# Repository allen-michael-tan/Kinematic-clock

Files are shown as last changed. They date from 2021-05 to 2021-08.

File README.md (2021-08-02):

# Kinematic Clock

This repository showcases how Singapore Polytechnic MakerSpace's kinematic clock was made.  

The design follows the Clockception instructables guide made by [madebymorgan](https://www.instructables.com/Clockception-How-to-Build-a-Clock-Made-From-Clocks/), where some aspects of the design were modified. 

## 3D Design

Before fabrication, all components were modelled in Autodesk Inventor Professional. The inventor files can be found [here](https://github.com/allen-michael-tan/Kinematic-clock/tree/main/Inventor%20files)

In this design, each digit will be represented using 6 individual smaller clocks, 24 clocks were needed to display 4 digits. The colour scheme used in the design is black and white.

### Clock design

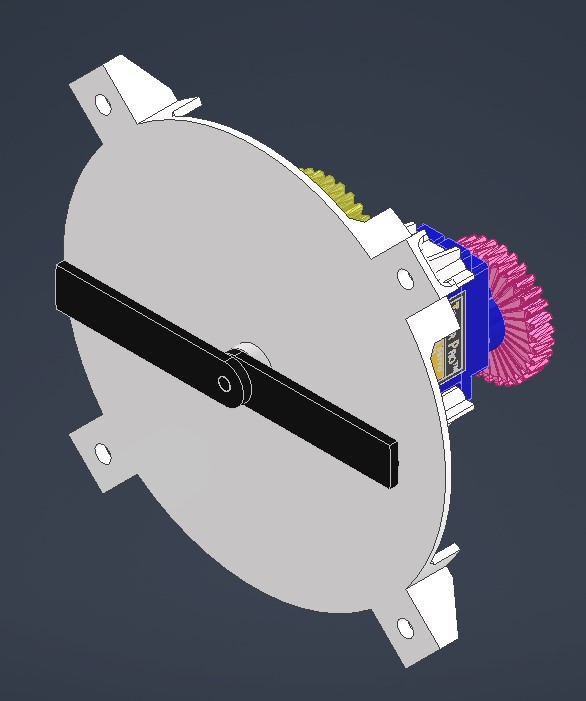
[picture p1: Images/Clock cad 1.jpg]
Clock cad 1
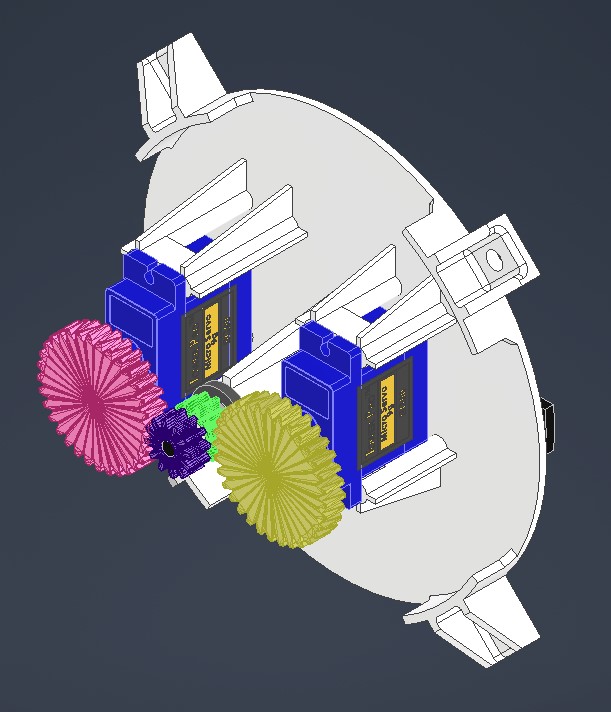
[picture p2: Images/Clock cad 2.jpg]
Clock cad 2
 

The design of the individual clock bodies is shown above. 

### Board design

In addition to having a board to mount the clocks onto, 4 smaller boards are included in the design to raise the board forward, giving it a floating illusion when mounted onto a wall. 

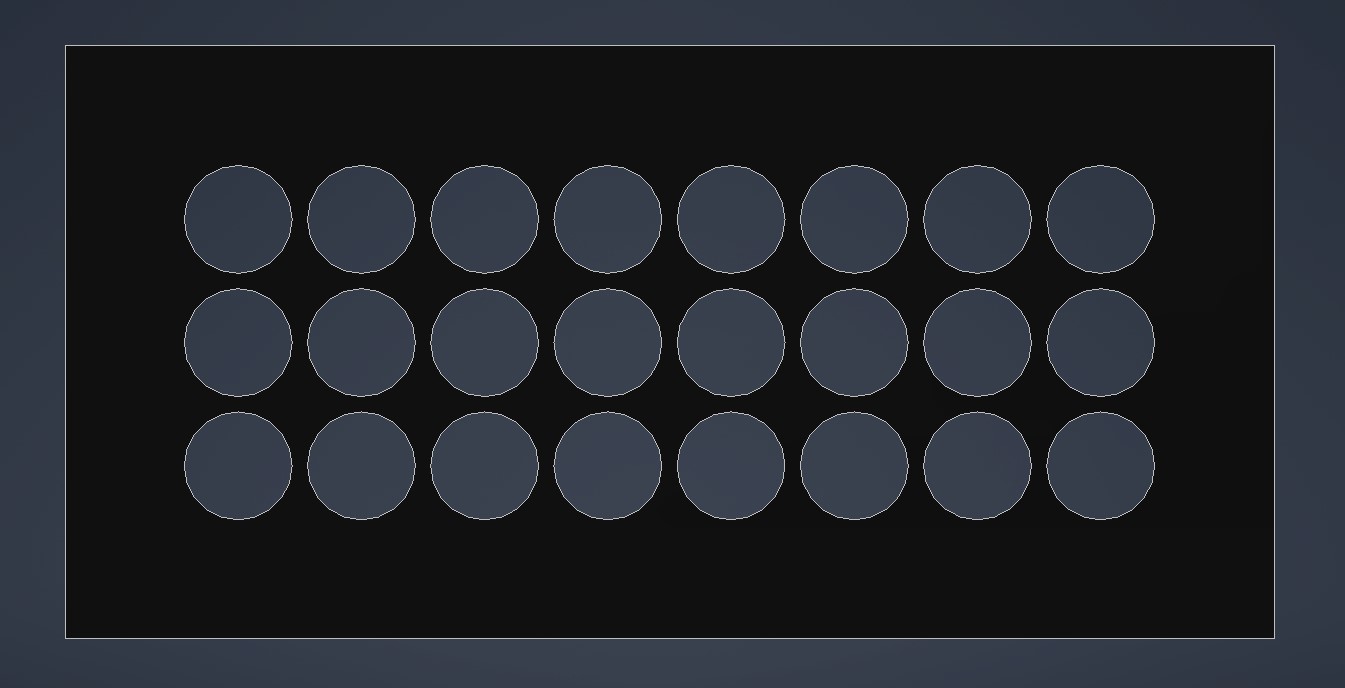
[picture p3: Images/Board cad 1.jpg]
Board cad 1


This is the front view of the board. 

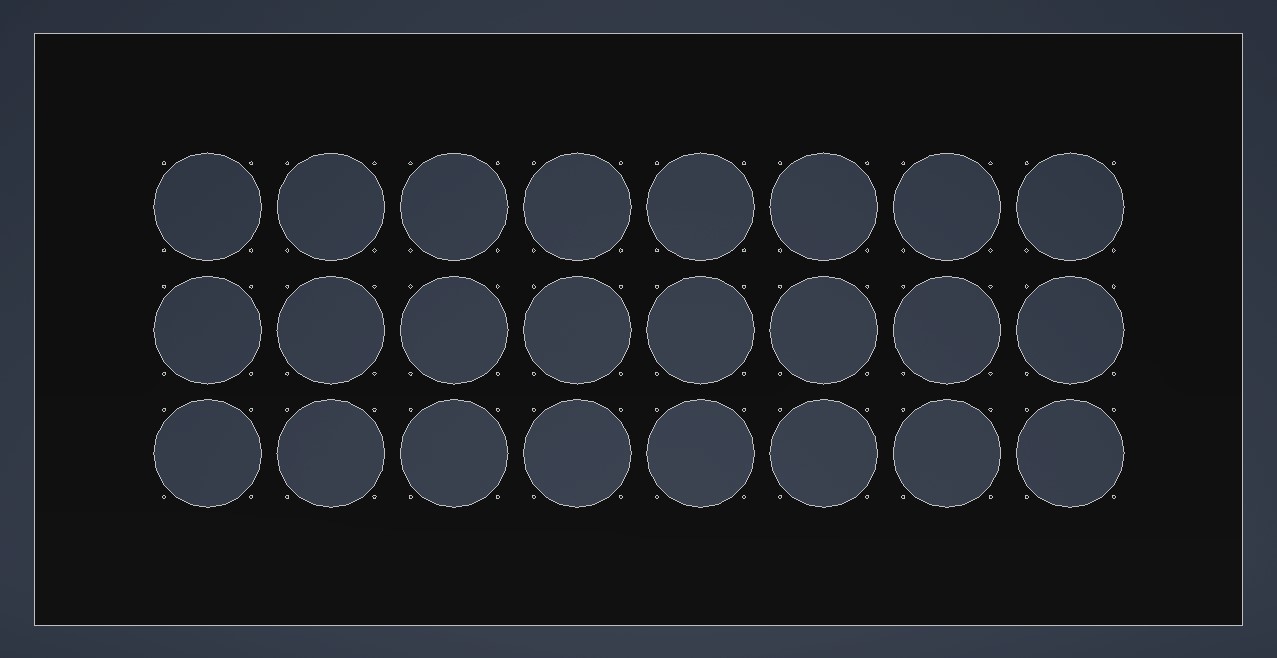
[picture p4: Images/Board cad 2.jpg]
Board cad 2


This is the back view of the board.

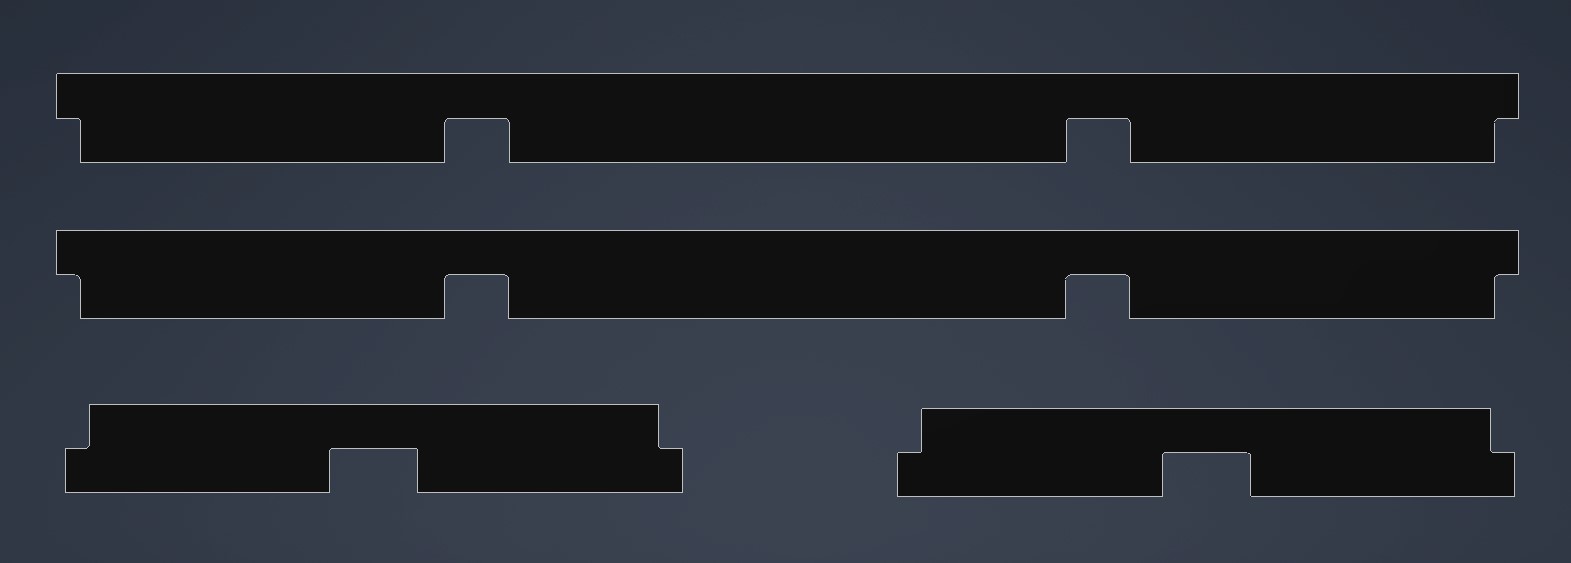
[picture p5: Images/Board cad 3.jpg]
Board cad 3


These are the smaller boards attached to the back of the main board, they are offseted inwards to give the floating illusion when the board is mounted onto a wall.

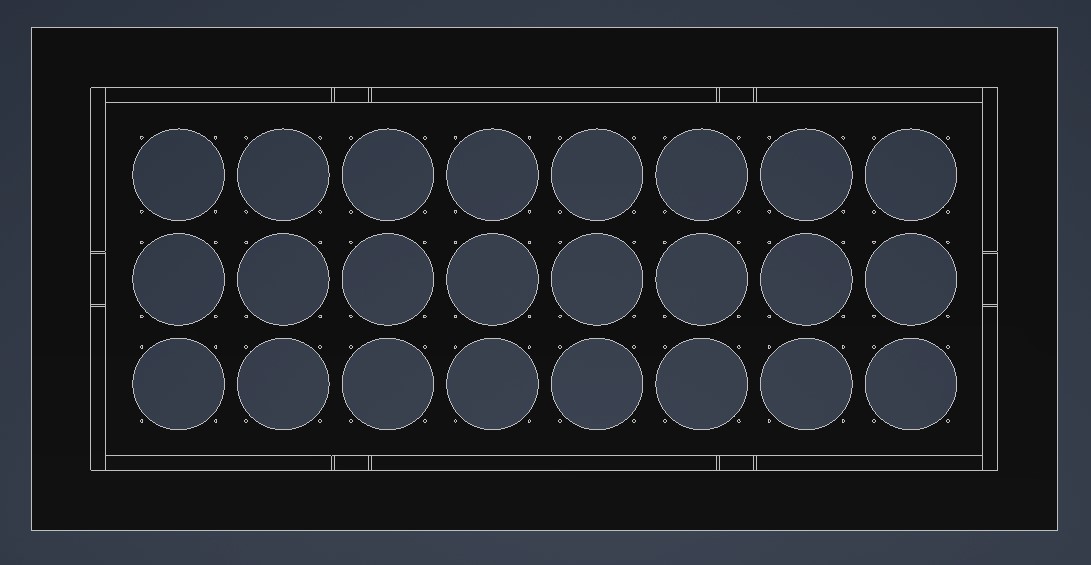
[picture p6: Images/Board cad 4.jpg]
Board cad 4


The above shows the assembly of the smaller boards onto the back of the main board. In the actual piece, they will be screwed into the main board using self tapping wood screws and L brackets. 

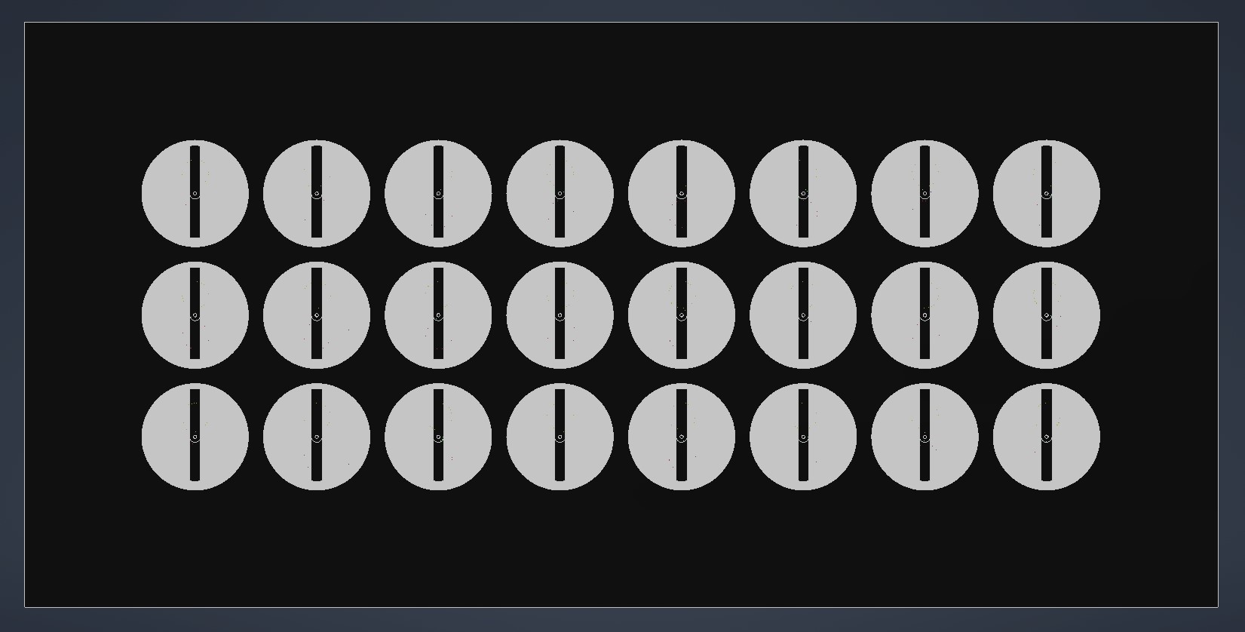
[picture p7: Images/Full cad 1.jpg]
Full cad 1


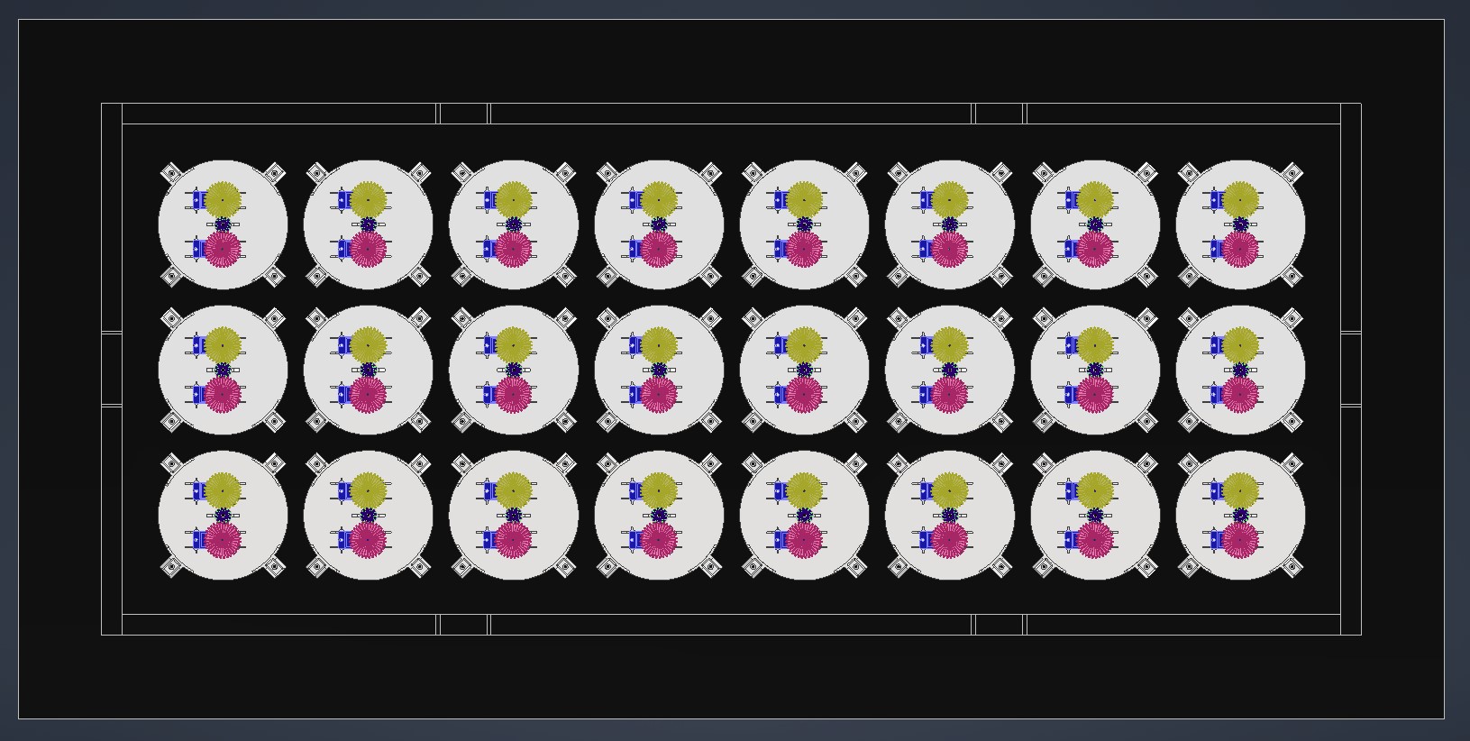
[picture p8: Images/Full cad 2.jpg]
Full cad 2


The above shows the respective front and back views of the full assembly of the kinematic clock in 3D CAD.

## Clock Assembly
Each clock is made up of: 

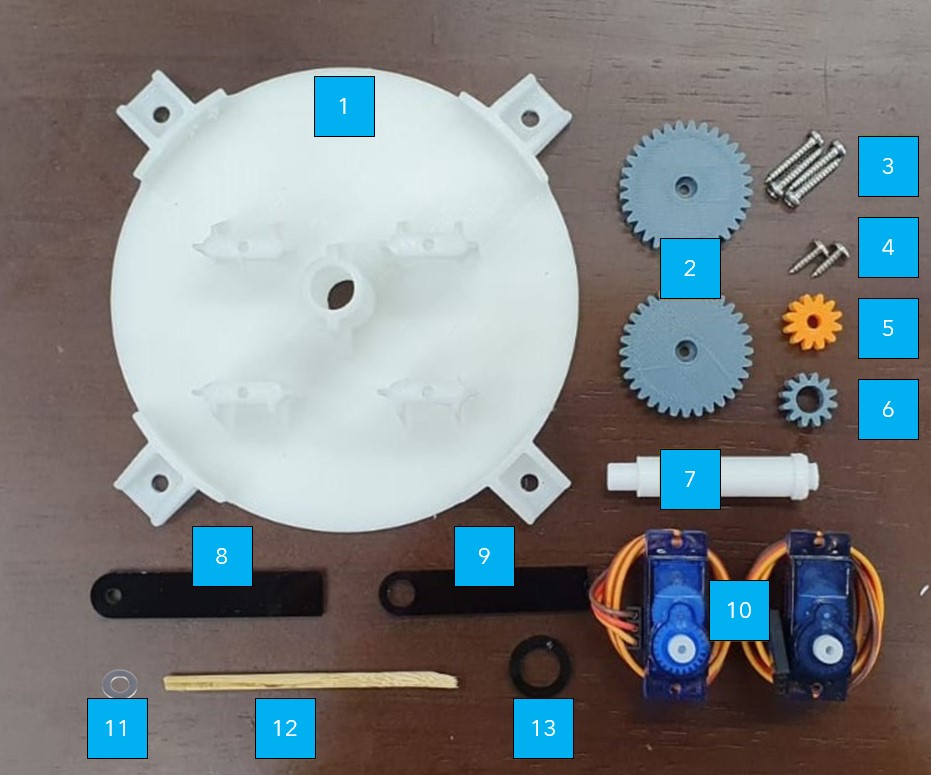
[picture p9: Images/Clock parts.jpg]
Clock parts


1. Clock body [1]
2. Servo gear [2]
3. M2x12 pan head self-tapping screw [4]
4. M2x8 flanged pan head self-tapping screw [2]
5. Minute hand gear [1]
6. Hour hand gear [1]
7. Hour hand shaft [1]
8. Minute hand [1]
9. Hour hand [1]
10. Continuous servo motor [2]
11. M3 plain washer [3]
12. Bamboo skewer [1]
13. Retaining ring [1]  

### Parts manufacturing

The components of each clock were created using 3D printers, laser cutters and vinyl stickers.

#### 3D print

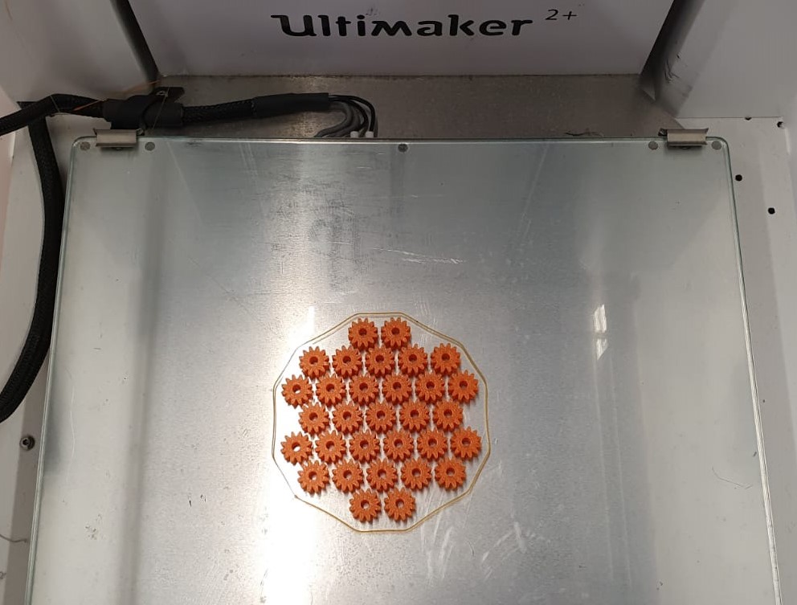
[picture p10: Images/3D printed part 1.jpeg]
3D printed part 1


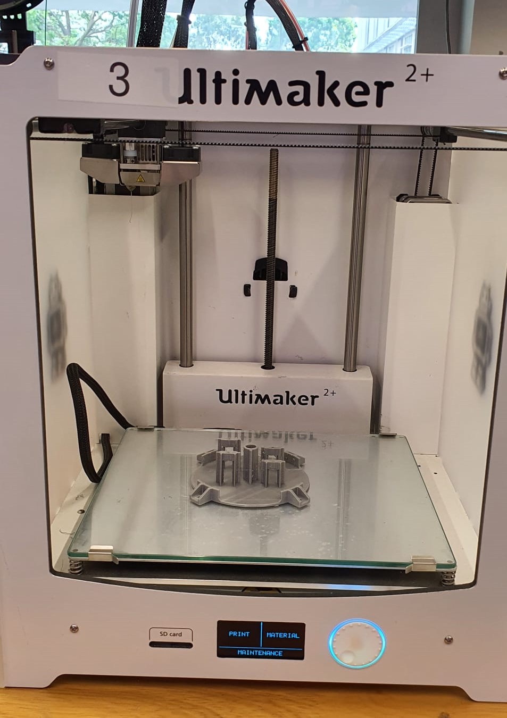
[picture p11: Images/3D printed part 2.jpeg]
3D printed part 2


Majority of the clock parts were 3D printed with PLA material.

#### Laser cut

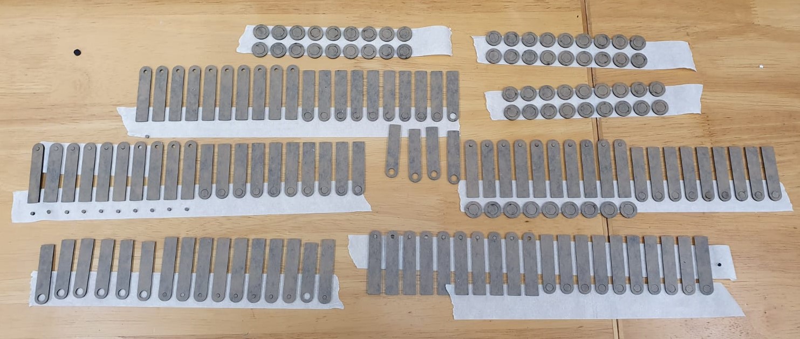
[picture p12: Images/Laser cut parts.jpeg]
Laser cut parts


Flat parts such as clock hands and hour retaining ring were made with laser cut 2mm black coloured acrylic. 

#### Vinyl sticker

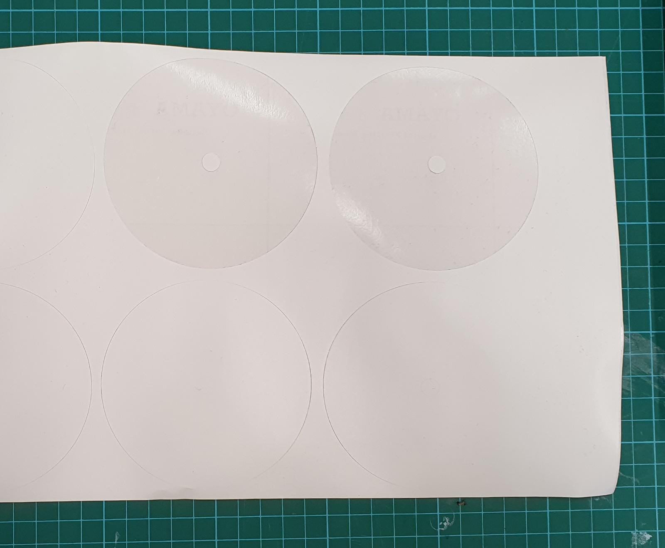
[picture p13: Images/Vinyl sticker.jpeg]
Vinyl sticker


In order to allow for uniformity across all the clock faces, white vinyl stickers were cut and applied onto each clock face. 

### Pre-assembly preparation

Before each clocks were put together, some components of the clock had to be prepared first.

#### Coating of 3D printed parts

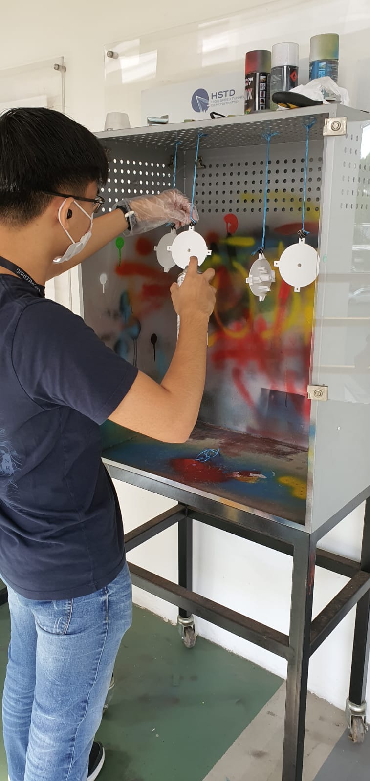
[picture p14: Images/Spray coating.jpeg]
Spray coating


The material used for all 3D printed parts was PLA. This material has the tendency to disintigrate after a period of time, so a clear coat was applied on all the printed parts to increase their longevity. 

#### Hour hand assembly

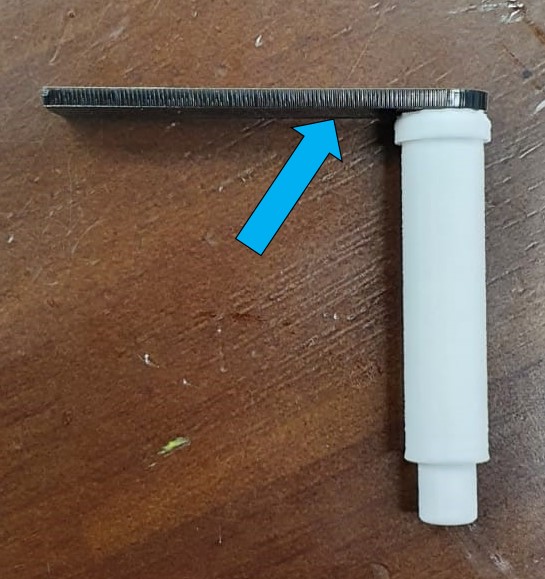
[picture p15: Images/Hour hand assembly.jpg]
Hour hand assembly


The laser cut hour hand (blue arrow) was superglued to the tip of the hour hand shaft as shown above.

#### Minute hand assembly

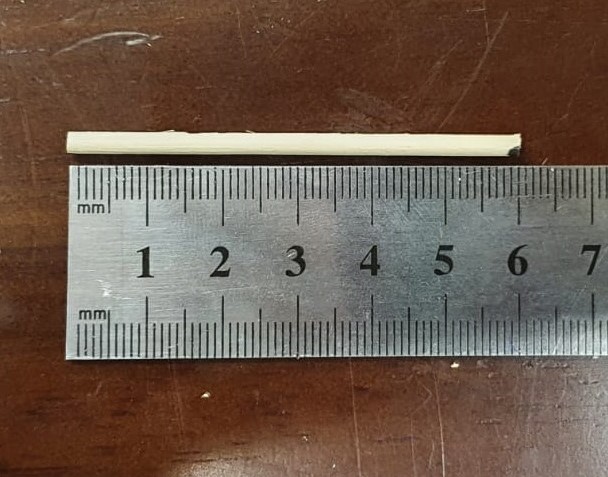
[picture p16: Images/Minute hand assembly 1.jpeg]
Minute hand assembly 1


3mm thick bamboo skewers were cut into lengths of 60mm.

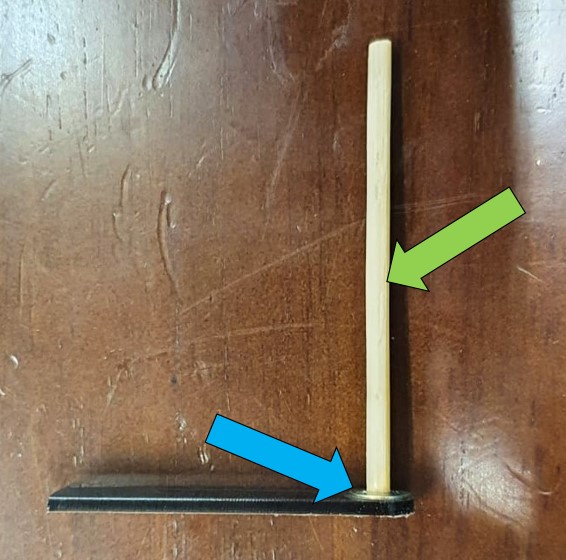
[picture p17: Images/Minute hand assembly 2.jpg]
Minute hand assembly 2


M3 plain washer was superglued to the underside of the laser cut minute hand (blue arrow), this is done so to minimize friction between the minute and hour hand as they rotate. 

After which, a bamboo skewer was inserted to the minute hand and superglued (green arrow).

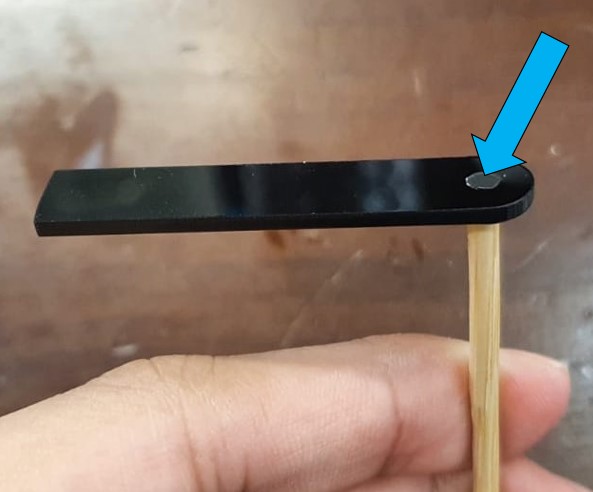
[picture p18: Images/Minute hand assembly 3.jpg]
Minute hand assembly 3


Lastly, on the other side of the minute hand where the bamboo skewer was inserted, black paint is applied onto the exposed side of the skewer (blue arrow). 

### Assembly

#### Step 1

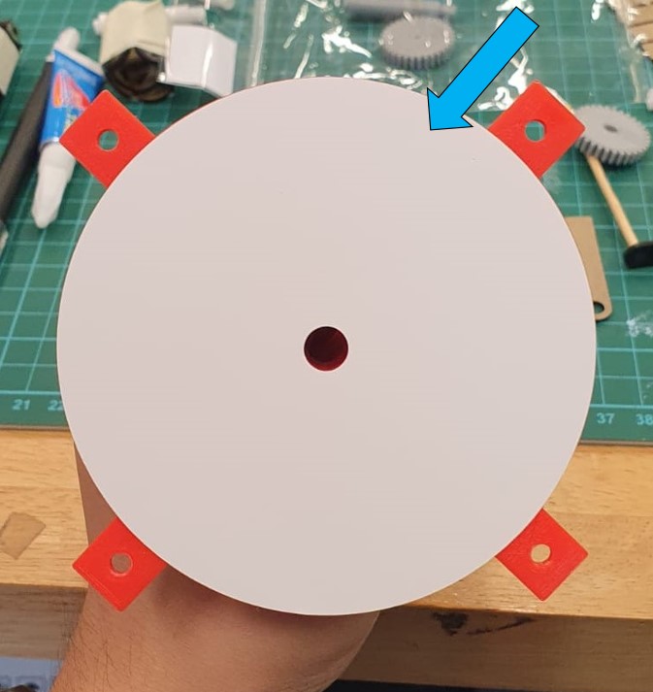
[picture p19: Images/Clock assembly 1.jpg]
Clock assembly 1


The colour theme of the clock was black and white - black board and clock hands, white clock face. As the clock bodies were printed in different colours, white vinyl stickers were cut out and pasted onto the outside face of the clock body (blue arrow). 

*****

#### Step 2

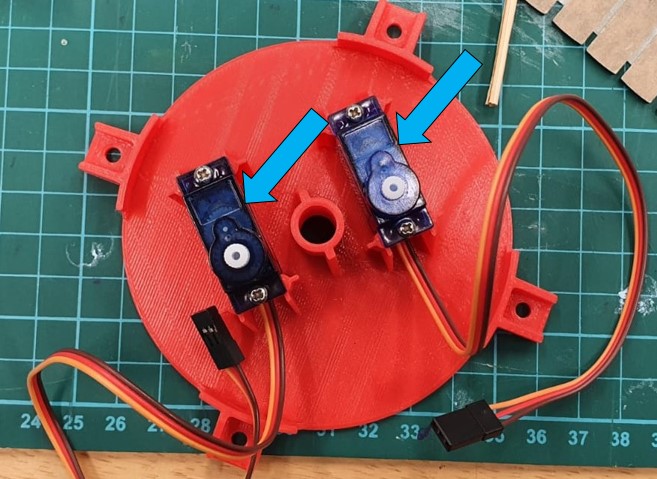
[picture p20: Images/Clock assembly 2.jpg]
Clock assembly 2


Next, two continuous servo motors were installed onto the clock body as shown above and secured using 4 screws (blue arrows).

*****

#### Step 3

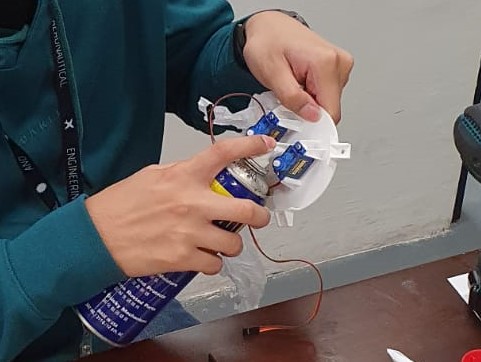
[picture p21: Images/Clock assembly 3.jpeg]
Clock assembly 3


Before inserting the hour hand, the shaft hub was lubricated using WD 40 to reduce friction between the hour hand shaft and the clock body.

*****

#### Step 4

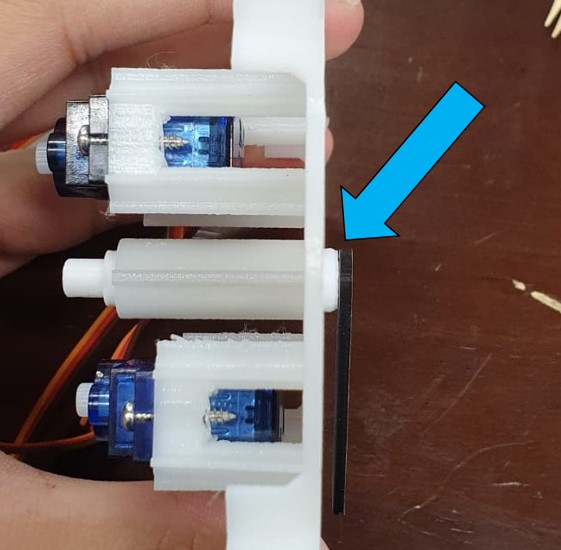
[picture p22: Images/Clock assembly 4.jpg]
Clock assembly 4


The hour hand was inserted as shown (blue arrow). 

*****

#### Step 5

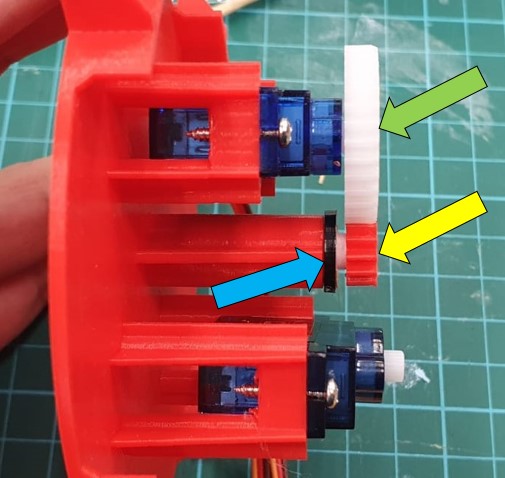
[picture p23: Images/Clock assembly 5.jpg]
Clock assembly 5


After the hour hand has been inserted, a retaining ring (blue arrow) was inserted as shown to prevent he hour hand from falling off. 

Following that, the hour hand gear (yellow arrow) and a servo gear (green arrow) was assembled accordingly. Then, a screw is used to secure the servo gear to the servo motor. 

*****

#### Step 6

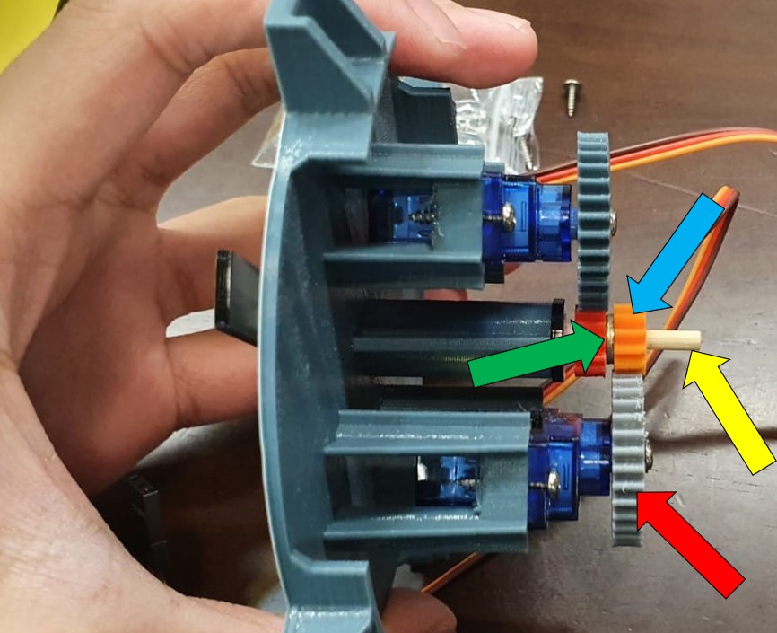
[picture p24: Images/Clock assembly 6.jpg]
Clock assembly 6


In this final step, the minute hand (yellow arrow) was inserted into the hour hand shaft, followed by two washers (green arrow) and minute hand gear (blue arrow).

It is important to note that, the before inserting the minute hand gear, the bamboo skewer should rotate freely with little friction whilst inserted in the hour hand shaft. This is because if there was too much friction, when the hour hand rotates, the minute hand will rotate along it which is undesired. 

The purpose of the washer is to prevent the bamboo skewer from jiggling in and out the hour hand shaft.

Lastly, a second servo gear (red arrow) is secured to the second servo motor with a screw as shown.  

## Board

The main board was made out of 15mm thick plywood. The parts were cut using a 2D CNC router. 

#### Step 1

The file of the boards were exported as dxf files then inserted into the versa cut software for the 2D CNC router to be prepared and cut. 

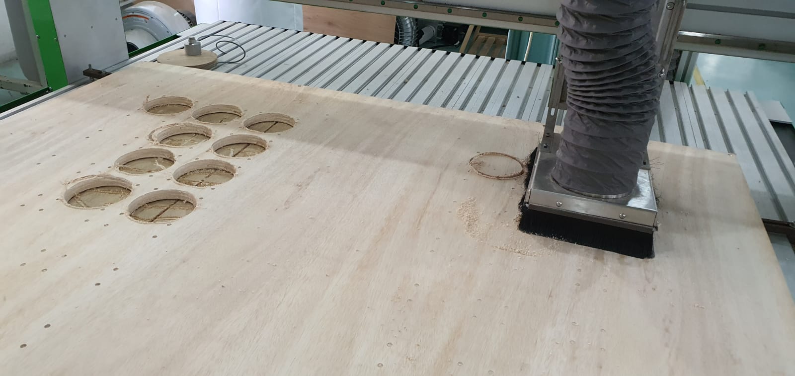
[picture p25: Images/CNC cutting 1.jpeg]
CNC cutting 1


2D router cutting the outline of the board.

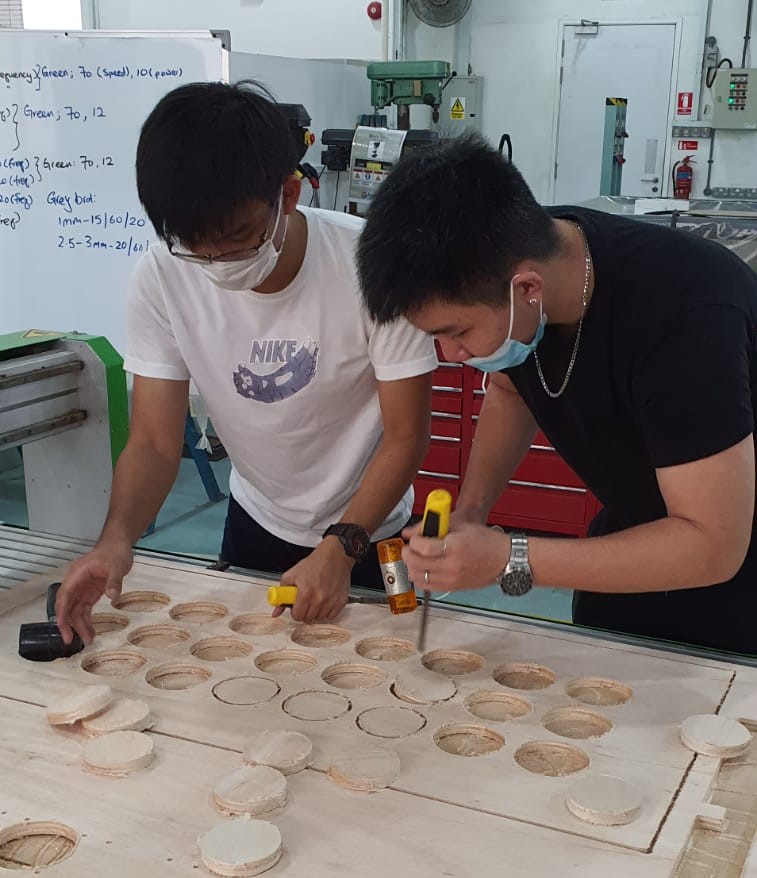
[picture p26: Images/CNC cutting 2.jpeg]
CNC cutting 2


Once the cutting was finished, pieces of the board were removed from the raw material by chiseling them out. 

****

#### Step 2

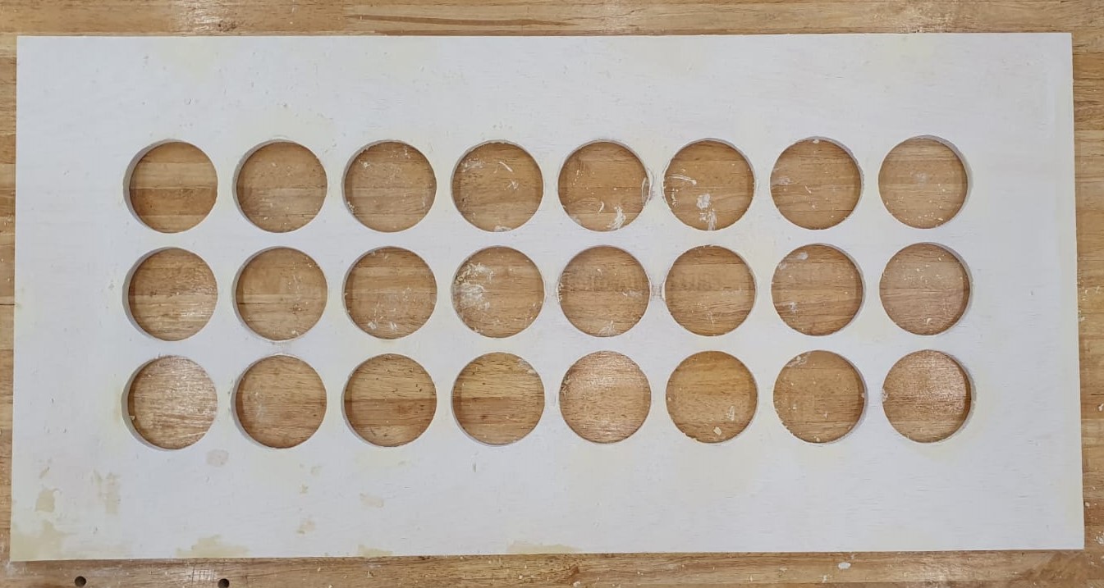
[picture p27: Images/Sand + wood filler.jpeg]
Sand + wood filler


The board pieces were repeatedly sanded to achieve a smooth finish, wood filler was applied to damaged areas that requried repairs. After applying the wood filler, the board pieces were sanded once more.

****

#### Step 3

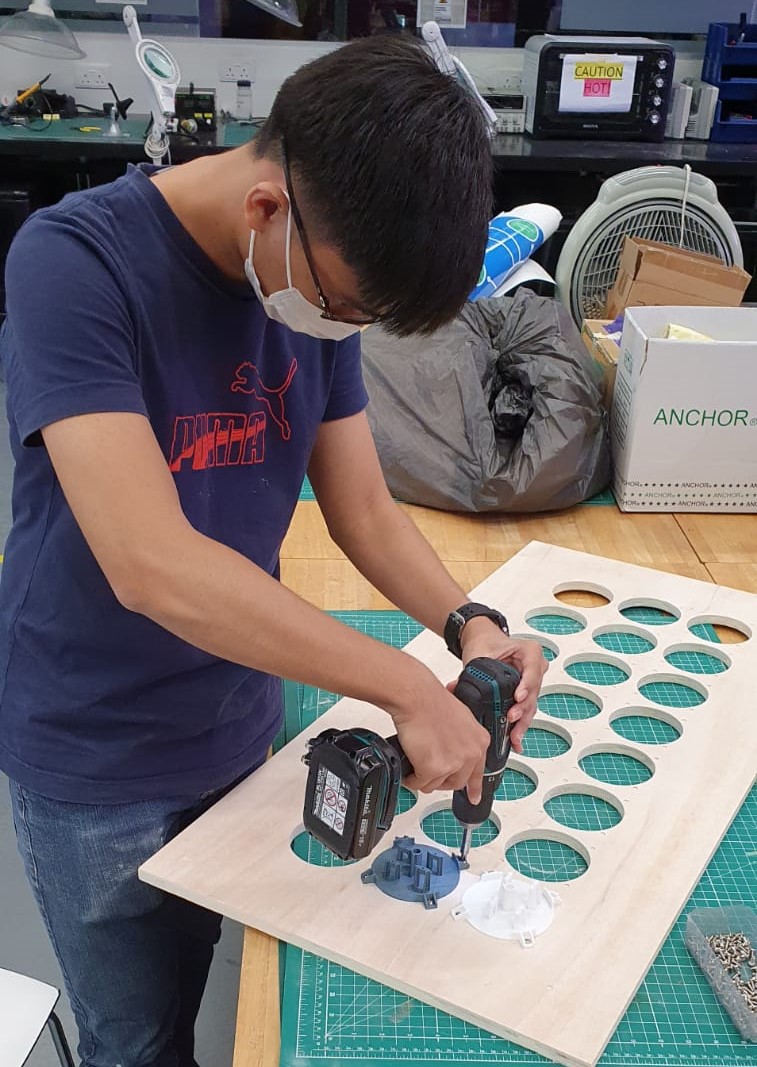
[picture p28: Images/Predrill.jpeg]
Predrill


Pilot holes for the mounting of the clocks were pre-drilled as shown.

****

#### Step 4

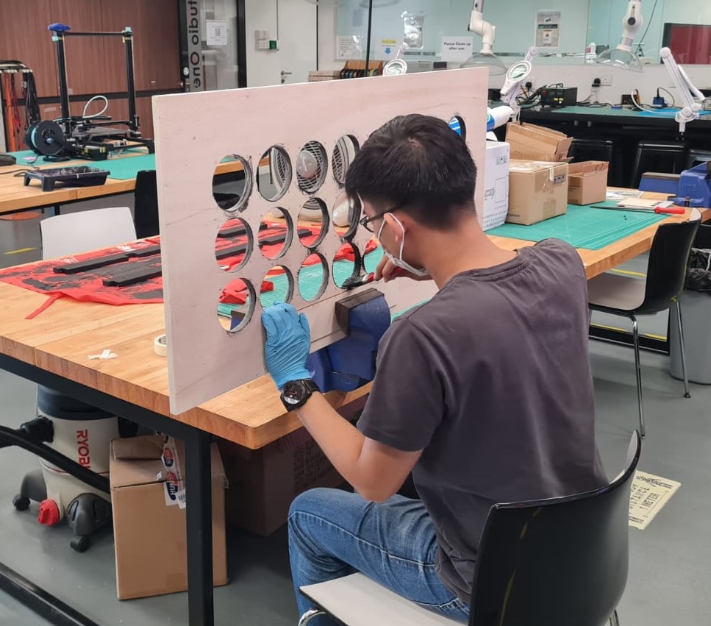
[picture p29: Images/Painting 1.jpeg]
Painting 1


Once the surface of the board pieces were sanded smooth and all necessary pilot holes were drilled, all pieces were hand painted in black colour. 

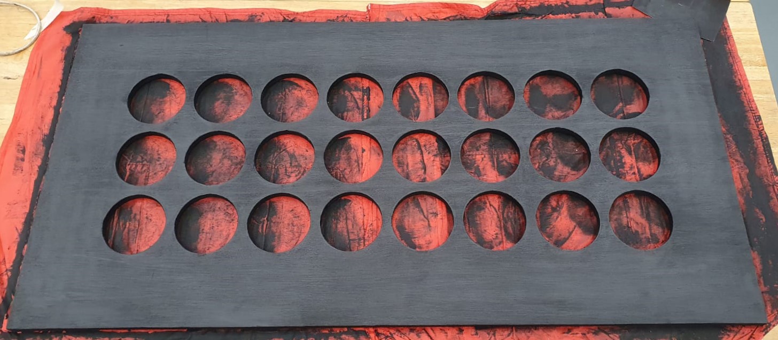
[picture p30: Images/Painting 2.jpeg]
Painting 2


A total of three coats were applied, with light sanding being done in between each coat of paint. 

****

#### Step 5

Once all the board pieces were painted black, two coats of clear lacquer was spray painted evenly on all the pieces to protect and give the wood a shiny finish. 

****

#### Step 6

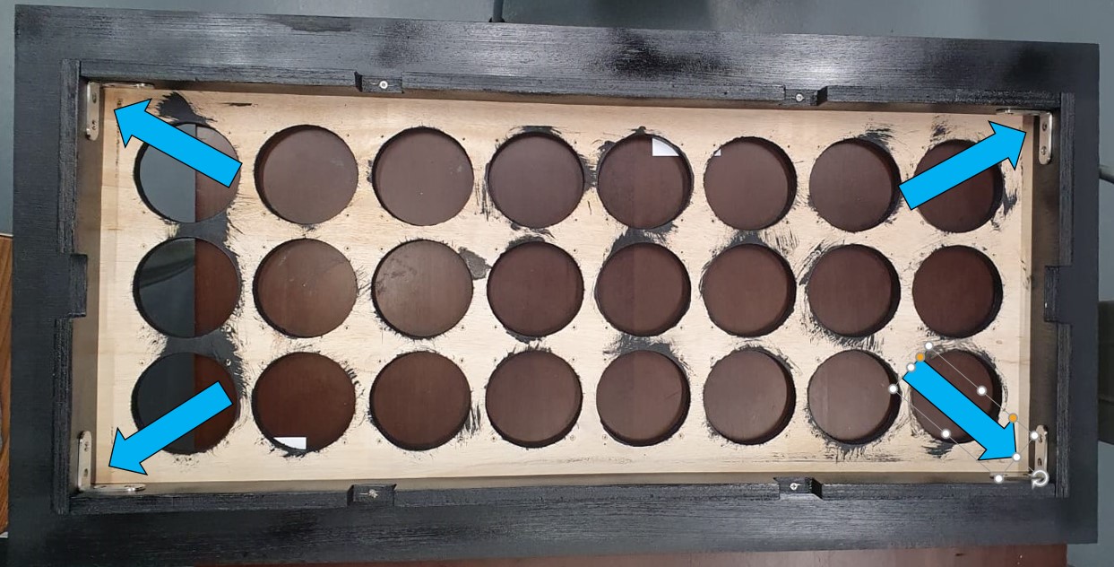
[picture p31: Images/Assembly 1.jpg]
Assembly 1


Once the lacquer had finished drying, it was time to assemble all the board pieces together. They are assembled as whown above. Wood screws were used to mount the smaller board pieces onto the main clock board. Furthermore, L brackets (blue arrows) were used to hold the smaller board pieces together. 

****

#### Step 7

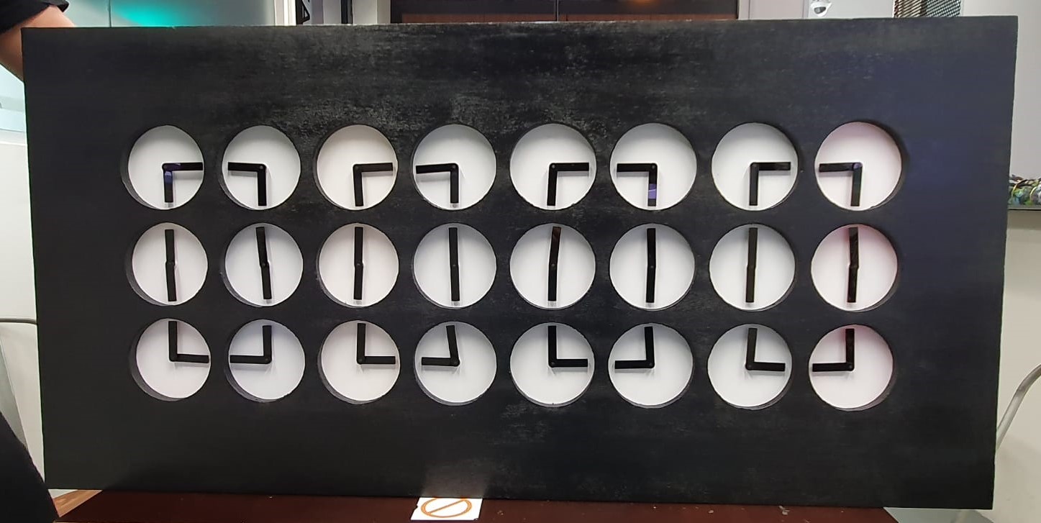
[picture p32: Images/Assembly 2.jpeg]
Assembly 2


Finally, all the clocks are screwed onto the back of the main board following the pre-drilled holes in step 3. 

****

#### Step 8

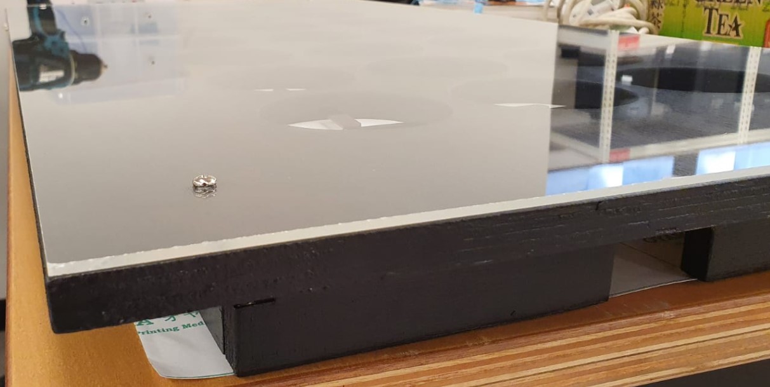
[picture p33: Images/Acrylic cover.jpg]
Acrylic cover


To protect the front side of clock, a 3mm clear piece of acrylic sheet was screwed onto the clock as a cover. 

## Wiring

To control the 48 servo motors, three PWM servo motor drivers were used. Modifications to the two of the three drivers were done before they could all be daisy-chained together.

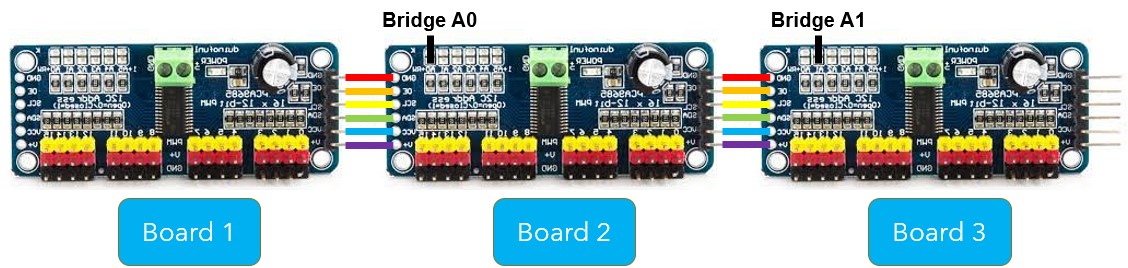
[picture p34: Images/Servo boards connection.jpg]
Servo boards connection


For board two, A0 was bridged; while for board three, A1 was bridged. The boards were then connected as shown.

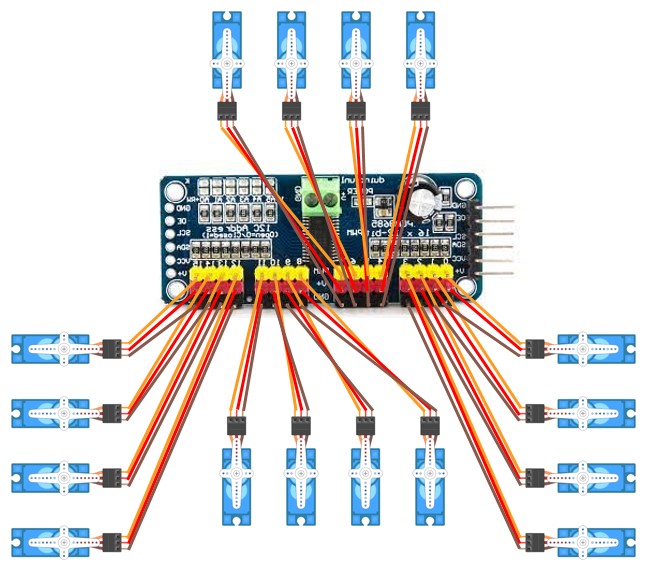
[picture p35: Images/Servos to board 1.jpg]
Servos to board 1


Each driver board will control 16 individual motors, its wiring to the board is as shown. The remaining motors were wired exactly the same way as this board.

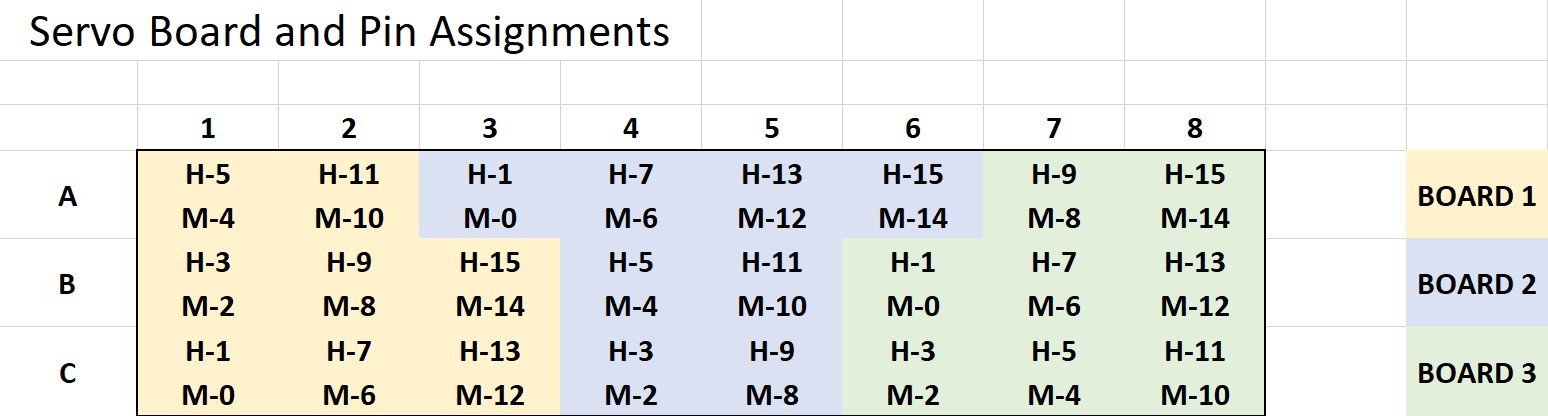
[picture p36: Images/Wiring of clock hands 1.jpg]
Wiring of clock hands 1


The servo motors of each individual minute and hour hands were wired to each resepctive boards with reference to the table above. "M" refers to minute hand while "H" refers to hour hand. 

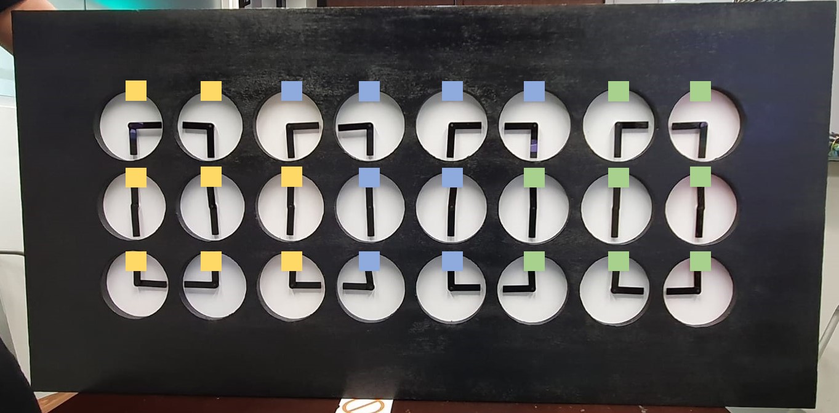
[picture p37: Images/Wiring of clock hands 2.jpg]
Wiring of clock hands 2


The above shows how the clocks are grouped from the front. 

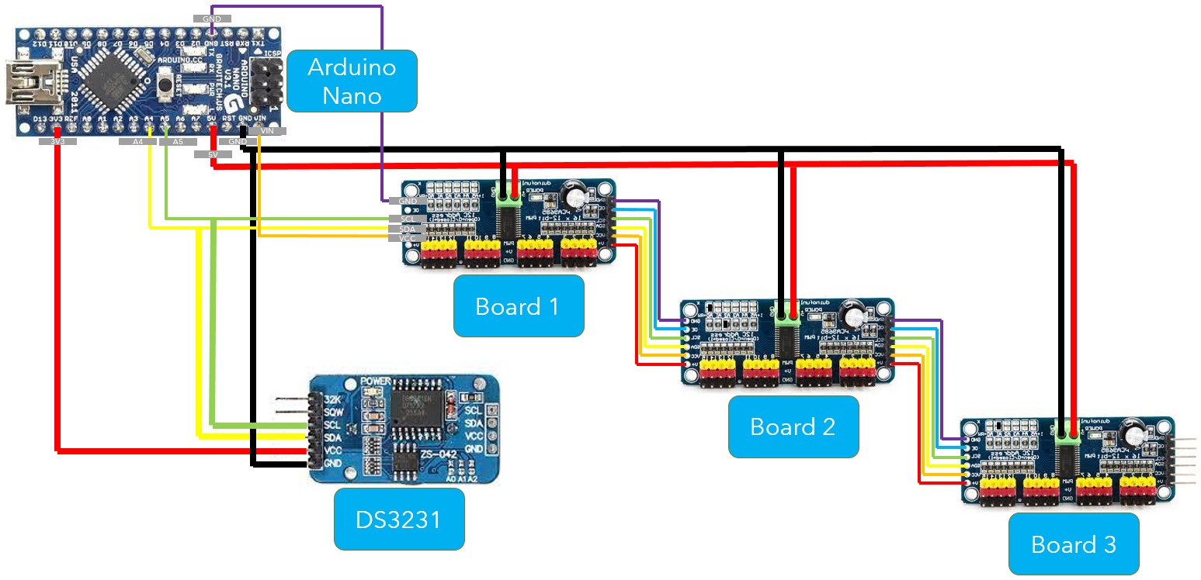
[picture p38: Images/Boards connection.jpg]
Boards connection


A real time clock (RTC) module, DS3231 was used to accurately calculate the time displayed by the servo motors. 

The wiring connection of all the different boards is as of above. *(click image to see which ports need to be connected.)*

Full schematic

This is the full schematic diagram of the kinematic clock.

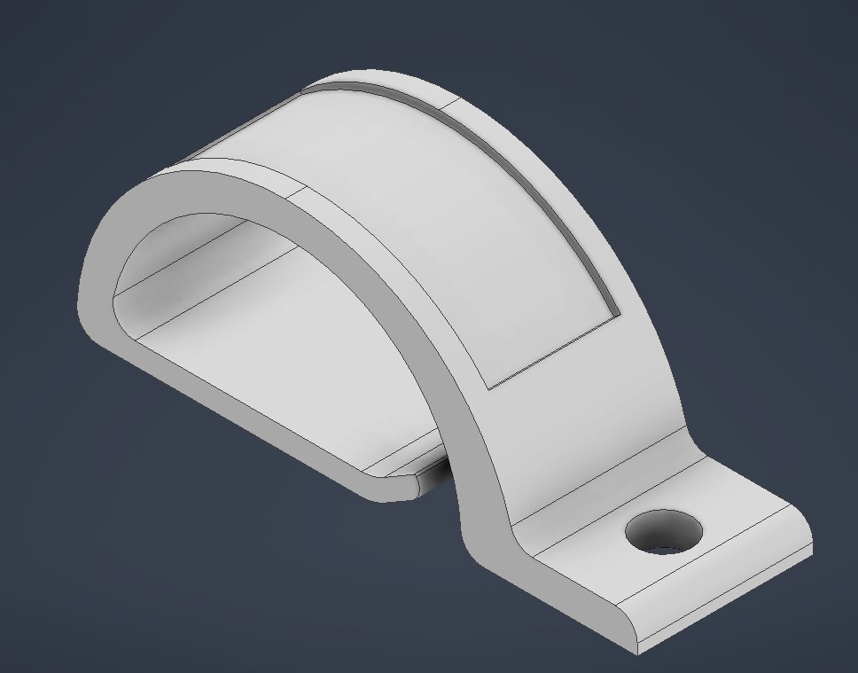
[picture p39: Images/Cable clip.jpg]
Cable clip


For cable management, cable organisers shown above was designed and 3D printed. It has a hole in the flat side where a screw can go through and secure it to the wood.

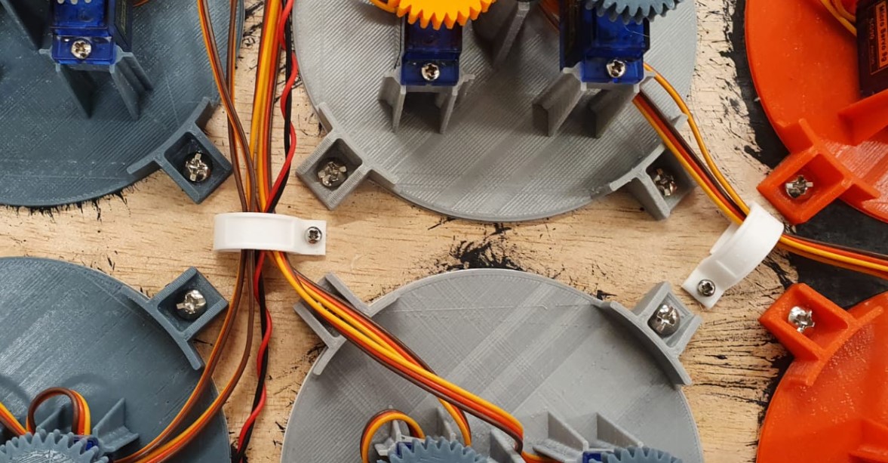
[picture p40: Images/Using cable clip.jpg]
Using cable clip


This was how the cable organisers were used.

Circuit board

A circuit board was made to make the system modular should any replacement work is needed.

Mounting of boards

All the different circuit boards were adhered onto the back of the board with double-sided foam tape. 

Final wiring

This is how the back of the clock looked like after everything is wired and assembled. 

## Programming

### Calibration

Before writing the full code of the clock, the position of each individual hands of each clocks were first calibrated. After that, another code is used to calibrate the numbers, ensuring the hands can display the desired digit as accurately as possible. 

#### Position calibration

	#include <Wire.h>
	#include <Adafruit_PWMServoDriver.h>
	
	Adafruit_PWMServoDriver board1 = Adafruit_PWMServoDriver(0x40);
	Adafruit_PWMServoDriver board2 = Adafruit_PWMServoDriver(0x41);
	Adafruit_PWMServoDriver board3 = Adafruit_PWMServoDriver(0x42);
	
	#define SERVOMIN  544 // This is the 'minimum' pulse length count (out of 4096)
	#define SERVOMAX  2400// This is the 'maximum' pulse length count (out of 4096)
	//#define USMIN  600 // This is the rounded 'minimum' microsecond length based on the minimum pulse of 150
	//#define USMAX  2400 // This is the rounded 'maximum' microsecond length based on the maximum pulse of 600
	#define SERVO_FREQ 50 // Analog servos run at ~50 Hz updates
	
	int number; // number command 
	
	void setup() {  
	
	  Serial.begin(9600); // initialize Serial connection
	  
	  board1.begin();  // Initialize servo ccontrol boards 
	  board2.begin();
	  board3.begin();
	  board1.setOscillatorFrequency(27000000);
	  board2.setOscillatorFrequency(27000000);
	  board3.setOscillatorFrequency(27000000);
	  board1.setPWMFreq(SERVO_FREQ);  // Analog servos run at ~50 Hz updates
	  board2.setPWMFreq(SERVO_FREQ); 
	  board3.setPWMFreq(SERVO_FREQ); 
	  
	  Serial.println("Ready for command");
	  
	  yield();
	}
	
	void loop() { 
	
	  while(Serial.available()>1){ // See if a command has been sent
	    number = Serial.parseInt(); // Turn command into integer
	    Serial.print(number);
	    Serial.println(" sent");
	    angleToPulse(number);
	  }
	  delay(100);
	}
	
	void angleToPulse(int ang){
	   int pulse1 = map(ang,0, 180, SERVOMIN,SERVOMAX); // Map angle of 0 to 180 to Servo min and Servo max 
	   int pulse2 = int(float(pulse1) / 1000000 * SERVO_FREQ * 4096);
	   Serial.print("Angle: ");Serial.print(ang);
	   Serial.print(" pulse: ");Serial.println(pulse2);
	   board1.setPWM(0 , 0, pulse2); // Change board number and servo number (first number in the bracket) based on which servo number and its corresponding board is being used.
	   delay(100);
	}

The above was the code used to calibrate the position of the hour and minute hands of the clocks. The process is explained below:

1. In the main void loop, the line - "board1.setPWM(0, 0, pulse2)" was modified constantly based on which clock's clock hand was being calibrated at the time. For example, if board two's (servo driver board) third servo is being calibrated, the line is as such - "board**2**.setPWM(**2**, 0, pulse2)".
2. The code was uploaded and run.
3. In the serial monitor, "Ready for command" was shown.
4. When a value of "120" was sent to the servo, the hour hand moved to its corresponding 120 position.
5. The hour hand was physically rotated towards the 12 o'clock position without rotating the servo motor.
6. After the hour hand was adjusted, a value of "80" was sent to the servo, where the hand moved in a clockwise direction.
6. Values between "120" and "80" were sent to the servo until the hour hand corresponded to 12 o'clock position accurately. That value was noted down in the [excel sheet](https://drive.google.com/file/d/1sLUSswgiBBg3gsoc3c7aR3SdEHQj8qRx/view?usp=sharing) in the C2 hour CCW column.
7. For the 3 o'clock position, values around "80" were modified until the hand correspnded to the 3 o'clock position from the clockwise direction accurately. That value was noted in the table's C2 hour CW column.
8. Similarly, for the 6 and 9 o'clock positions, values around "40" and "10" were sent to the servo until the values of the desired positions for both timings were obtained and noted in the C2 hour CW column for 6 and 9 o'clock respectively.
9. The 7.5 o'clock position was automatically calculated once the 6 and 9 o'clock positions were obtained.
10. Since all the 3D printed gears were not perfect, steps 5 to 10 were repeated in the counter clockwise direction.
11. Once the first hour hand was calibrated, steps 1 to 10 were repeated for the next minute hand.
12. Finally steps 1 - 11 were repeated for the remaining 23 clocks.  

**Note: In the table of the excel sheet, some cells are greyed out, this is because those particular positions will not be needed.**

Incomplete table

This was the table in the excel sheet before calibration.

Completed table

The completed table is shown above.

#### Number calibration

	#include <Wire.h>
	#include <Adafruit_PWMServoDriver.h>
	
	Adafruit_PWMServoDriver board1 = Adafruit_PWMServoDriver(0x40);
	Adafruit_PWMServoDriver board2 = Adafruit_PWMServoDriver(0x41);
	Adafruit_PWMServoDriver board3 = Adafruit_PWMServoDriver(0x42);
	
	#define SERVOMIN  544 // This is the 'minimum' pulse length count (out of 4096)
	#define SERVOMAX  2400// This is the 'maximum' pulse length count (out of 4096)
	//#define USMIN  600 // This is the rounded 'minimum' microsecond length based on the minimum pulse of 150
	//#define USMAX  2400 // This is the rounded 'maximum' microsecond length based on the maximum pulse of 600
	#define SERVO_FREQ 50 // Analog servos run at ~50 Hz updates
	
	int number; // Number command 
	
	void setup() {  
	
	  Serial.begin(9600); 
	  
	  board1.begin();  // Initialize servo ccontrol boards 
	  board2.begin();
	  board3.begin();
	  board1.setOscillatorFrequency(27000000);
	  board2.setOscillatorFrequency(27000000);
	  board3.setOscillatorFrequency(27000000);
	  board1.setPWMFreq(SERVO_FREQ);  // Analog servos run at ~50 Hz updates
	  board2.setPWMFreq(SERVO_FREQ); 
	  board3.setPWMFreq(SERVO_FREQ); 
	  
	  Serial.println("Ready for command");
	  
	  yield();
	}
	
	void loop() {  
	
	  while(Serial.available()>0){  // See if a command has been sent
	    number = Serial.parseInt(); // Turn command into integer
	    Serial.print(number);
	    Serial.println(" sent");
	    digit2(number); // Change between digit1 - digit4, depending on which digit is being calibrated
	  }
	  delay(1000);
	}
	
	int angleToPulse(int ang){
	  int pulse1 = map(ang,0, 180, SERVOMIN,SERVOMAX); // Map angle of 0 to 180 to Servo min and Servo max 
	  int pulse2 = int(float(pulse1) / 1000000 * SERVO_FREQ * 4096);
	  Serial.print("Angle: ");Serial.print(ang);
	  Serial.print(" pulse: ");Serial.println(pulse2);
	  return pulse2;
	}
	
	/*1st digit*/
	
	void digit1(int number) {
	  if (number == 11) {
	    board1.setPWM(5, 0, angleToPulse(72));delay(200);
	    board1.setPWM(4, 0, angleToPulse(40));delay(200);
	    board1.setPWM(3, 0, angleToPulse(116));delay(200);
	    board1.setPWM(2, 0, angleToPulse(40));delay(200);
	    board1.setPWM(1, 0, angleToPulse(119));delay(200);
	    board1.setPWM(0, 0, angleToPulse(88));delay(200);
	    board1.setPWM(11, 0, angleToPulse(53));delay(200);
	    board1.setPWM(10, 0, angleToPulse(8));delay(200);
	    board1.setPWM(9, 0, angleToPulse(110));delay(200);
	    board1.setPWM(8, 0, angleToPulse(38));delay(200);
	    board1.setPWM(7, 0, angleToPulse(120));delay(200);
	    board1.setPWM(6, 0, angleToPulse(16));delay(200);
	  }
	  else if (number == 1) {
	    board1.setPWM(5, 0, angleToPulse(16));delay(200);
	    board1.setPWM(4, 0, angleToPulse(19));delay(200);
	    board1.setPWM(3, 0, angleToPulse(20));delay(200);
	    board1.setPWM(2, 0, angleToPulse(19));delay(200);
	    board1.setPWM(1, 0, angleToPulse(19));delay(200);
	    board1.setPWM(0, 0, angleToPulse(30));delay(200);
	    board1.setPWM(11, 0, angleToPulse(52));delay(200);
	    board1.setPWM(10, 0, angleToPulse(41));delay(200);
	    board1.setPWM(9, 0, angleToPulse(110));delay(200);
	    board1.setPWM(8, 0, angleToPulse(38));delay(200);
	    board1.setPWM(7, 0, angleToPulse(120));delay(200);
	    board1.setPWM(6, 0, angleToPulse(125));delay(200);
	  }
	  else if (number == 2) {
	    board1.setPWM(5, 0, angleToPulse(73));delay(200); 
	    board1.setPWM(4, 0, angleToPulse(76));delay(200);
	    board1.setPWM(3, 0, angleToPulse(79));delay(200);
	    board1.setPWM(2, 0, angleToPulse(39));delay(200);
	    board1.setPWM(1, 0, angleToPulse(119));delay(200);
	    board1.setPWM(0, 0, angleToPulse(88));delay(200);
	    board1.setPWM(11, 0, angleToPulse(53));delay(200); 
	    board1.setPWM(10, 0, angleToPulse(8));delay(200);
	    board1.setPWM(9, 0, angleToPulse(112));delay(200);
	    board1.setPWM(8, 0, angleToPulse(1));delay(200);
	    board1.setPWM(7, 0, angleToPulse(15));delay(200);
	    board1.setPWM(6, 0, angleToPulse(16));delay(200);
	  }
	}
	
	/*2nd digit*/
	
	void digit2(int number) {
	  if (number == 11) {
	    board2.setPWM(1, 0, angleToPulse(88));delay(200); 
	    board2.setPWM(0, 0, angleToPulse(46));delay(200); 
	    board1.setPWM(15, 0, angleToPulse(120));delay(200); 
	    board1.setPWM(14, 0, angleToPulse(45));delay(200); 
	    board1.setPWM(13, 0, angleToPulse(119));delay(200); 
	    board1.setPWM(12, 0, angleToPulse(78));delay(200);
	    board2.setPWM(7, 0, angleToPulse(44));delay(200);
	    board2.setPWM(6, 0, angleToPulse(6));delay(200);
	    board2.setPWM(5, 0, angleToPulse(122));delay(200); 
	    board2.setPWM(4, 0, angleToPulse(46));delay(200);
	    board2.setPWM(3, 0, angleToPulse(124));delay(200);
	    board2.setPWM(2, 0, angleToPulse(14));delay(200);
	  }
	  else if (number == 1) {
	    board2.setPWM(1, 0, angleToPulse(33));delay(200);
	    board2.setPWM(0, 0, angleToPulse(29));delay(200);
	    board1.setPWM(15, 0, angleToPulse(25));delay(200);
	    board1.setPWM(14, 0, angleToPulse(26));delay(200); 
	    board1.setPWM(13, 0, angleToPulse(27));delay(200);
	    board1.setPWM(12, 0, angleToPulse(21));delay(200); 
	    board2.setPWM(7, 0, angleToPulse(44));delay(200);  
	    board2.setPWM(6, 0, angleToPulse(37));delay(200); 
	    board2.setPWM(5, 0, angleToPulse(122));delay(200); 
	    board2.setPWM(4, 0, angleToPulse(46));delay(200); 
	    board2.setPWM(3, 0, angleToPulse(125));delay(200); 
	    board2.setPWM(2, 0, angleToPulse(120));delay(200);
	  }
	  else if (number == 2) {
	    board2.setPWM(1, 0, angleToPulse(87));delay(200); 
	    board2.setPWM(0, 0, angleToPulse(79));delay(200); 
	    board1.setPWM(15, 0, angleToPulse(81));delay(200);
	    board1.setPWM(14, 0, angleToPulse(44));delay(200); 
	    board1.setPWM(13, 0, angleToPulse(119));delay(200); 
	    board1.setPWM(12, 0, angleToPulse(83));delay(200); 
	    board2.setPWM(7, 0, angleToPulse(44));delay(200);
	    board2.setPWM(6, 0, angleToPulse(7));delay(200);
	    board2.setPWM(5, 0, angleToPulse(122));delay(200);
	    board2.setPWM(4, 0, angleToPulse(11));delay(200);
	    board2.setPWM(3, 0, angleToPulse(18));delay(200); 
	    board2.setPWM(2, 0, angleToPulse(14));delay(200);
	  }
	  else if (number == 3) {
	    board2.setPWM(1, 0, angleToPulse(87));delay(200);
	    board2.setPWM(0, 0, angleToPulse(79));delay(200);
	    board1.setPWM(15, 0, angleToPulse(82));delay(200); 
	    board1.setPWM(14, 0, angleToPulse(79));delay(200);
	    board1.setPWM(13, 0, angleToPulse(79));delay(200); 
	    board1.setPWM(12, 0, angleToPulse(84));delay(200); 
	    board2.setPWM(7, 0, angleToPulse(44));delay(200); 
	    board2.setPWM(6, 0, angleToPulse(7));delay(200);  
	    board2.setPWM(5, 0, angleToPulse(122));delay(200); 
	    board2.setPWM(4, 0, angleToPulse(11));delay(200); 
	    board2.setPWM(3, 0, angleToPulse(124));delay(200);
	    board2.setPWM(2, 0, angleToPulse(13));delay(200); 
	  }
	  else if (number == 4) {
	    board2.setPWM(1, 0, angleToPulse(53));delay(200);
	    board2.setPWM(0, 0, angleToPulse(47));delay(200);
	    board1.setPWM(15, 0, angleToPulse(119));delay(200); 
	    board1.setPWM(14, 0, angleToPulse(79));delay(200);
	    board1.setPWM(13, 0, angleToPulse(27));delay(200);
	    board1.setPWM(12, 0, angleToPulse(20));delay(200);
	    board2.setPWM(7, 0, angleToPulse(44));delay(200); 
	    board2.setPWM(6, 0, angleToPulse(37));delay(200); 
	    board2.setPWM(5, 0, angleToPulse(122));delay(200);
	    board2.setPWM(4, 0, angleToPulse(45));delay(200); 
	    board2.setPWM(3, 0, angleToPulse(125));delay(200); 
	    board2.setPWM(2, 0, angleToPulse(120));delay(200);
	  }
	  else if (number == 5) {
	    board2.setPWM(1, 0, angleToPulse(88));delay(200); 
	    board2.setPWM(0, 0, angleToPulse(45));delay(200); 
	    board1.setPWM(15, 0, angleToPulse(119));delay(200); 
	    board1.setPWM(14, 0, angleToPulse(80));delay(200); 
	    board1.setPWM(13, 0, angleToPulse(78));delay(200);
	    board1.setPWM(12, 0, angleToPulse(82));delay(200); 
	    board2.setPWM(7, 0, angleToPulse(12));delay(200);
	    board2.setPWM(6, 0, angleToPulse(7));delay(200);
	    board2.setPWM(5, 0, angleToPulse(49));delay(200); 
	    board2.setPWM(4, 0, angleToPulse(11));delay(200); 
	    board2.setPWM(3, 0, angleToPulse(124));delay(200); 
	    board2.setPWM(2, 0, angleToPulse(14));delay(200); 
	  }
	  else if (number == 6) {
	    board2.setPWM(1, 0, angleToPulse(88));delay(200);
	    board2.setPWM(0, 0, angleToPulse(45));delay(200);
	    board1.setPWM(15, 0, angleToPulse(120));delay(200);
	    board1.setPWM(14, 0, angleToPulse(44));delay(200); 
	    board1.setPWM(13, 0, angleToPulse(120));delay(200); 
	    board1.setPWM(12, 0, angleToPulse(78));delay(200);
	    board2.setPWM(7, 0, angleToPulse(12));delay(200);
	    board2.setPWM(6, 0, angleToPulse(7));delay(200);
	    board2.setPWM(5, 0, angleToPulse(49));delay(200); 
	    board2.setPWM(4, 0, angleToPulse(11));delay(200);
	    board2.setPWM(3, 0, angleToPulse(124));delay(200);
	    board2.setPWM(2, 0, angleToPulse(14));delay(200); 
	  }
	  else if (number == 7) {
	    board2.setPWM(1, 0, angleToPulse(87));delay(200);
	    board2.setPWM(0, 0, angleToPulse(79));delay(200);
	    board1.setPWM(15, 0, angleToPulse(25));delay(200);
	    board1.setPWM(14, 0, angleToPulse(26));delay(200);
	    board1.setPWM(13, 0, angleToPulse(27));delay(200);
	    board1.setPWM(12, 0, angleToPulse(21));delay(200);
	    board2.setPWM(7, 0, angleToPulse(43));delay(200);
	    board2.setPWM(6, 0, angleToPulse(6));delay(200); 
	    board2.setPWM(5, 0, angleToPulse(122));delay(200);
	    board2.setPWM(4, 0, angleToPulse(45));delay(200); 
	    board2.setPWM(3, 0, angleToPulse(125));delay(200);
	    board2.setPWM(2, 0, angleToPulse(120));delay(200);
	  }
	  else if (number == 8) {
	    board2.setPWM(1, 0, angleToPulse(88));delay(200);
	    board2.setPWM(0, 0, angleToPulse(46));delay(200);
	    board1.setPWM(15, 0, angleToPulse(120));delay(200);
	    board1.setPWM(14, 0, angleToPulse(80));delay(200); 
	    board1.setPWM(13, 0, angleToPulse(119));delay(200); 
	    board1.setPWM(12, 0, angleToPulse(83));delay(200);
	    board2.setPWM(7, 0, angleToPulse(44));delay(200); 
	    board2.setPWM(6, 0, angleToPulse(6));delay(200); 
	    board2.setPWM(5, 0, angleToPulse(122));delay(200); 
	    board2.setPWM(4, 0, angleToPulse(11));delay(200);
	    board2.setPWM(3, 0, angleToPulse(124));delay(200);
	    board2.setPWM(2, 0, angleToPulse(14));delay(200);
	  }
	  else if (number == 9) {
	    board2.setPWM(1, 0, angleToPulse(88));delay(200); 
	    board2.setPWM(0, 0, angleToPulse(46));delay(200);
	    board1.setPWM(15, 0, angleToPulse(120));delay(200);
	    board1.setPWM(14, 0, angleToPulse(80));delay(200);
	    board1.setPWM(13, 0, angleToPulse(79));delay(200); 
	    board1.setPWM(12, 0, angleToPulse(84));delay(200);
	    board2.setPWM(7, 0, angleToPulse(44));delay(200);
	    board2.setPWM(6, 0, angleToPulse(6));delay(200);
	    board2.setPWM(5, 0, angleToPulse(122));delay(200); 
	    board2.setPWM(4, 0, angleToPulse(45));delay(200); 
	    board2.setPWM(3, 0, angleToPulse(124));delay(200);
	    board2.setPWM(2, 0, angleToPulse(14));delay(200);
	  }
	}
	
	/*3rd digit*/
	
	void digit3(int number) {
	  if (number == 0) {
	    board2.setPWM(13, 0, angleToPulse(86.5));delay(200);
	    board2.setPWM(12, 0, angleToPulse(53));delay(200);
	    board2.setPWM(11, 0, angleToPulse(120));delay(200);
	    board2.setPWM(10, 0, angleToPulse(52));delay(200);
	    board2.setPWM(9, 0, angleToPulse(124));delay(200);
	    board2.setPWM(8, 0, angleToPulse(85));delay(200);
	    board2.setPWM(15, 0, angleToPulse(43));delay(200);
	    board2.setPWM(14, 0, angleToPulse(18));delay(200); 
	    board3.setPWM(1, 0, angleToPulse(122));delay(200);
	    board3.setPWM(0, 0, angleToPulse(46));delay(200);
	    board3.setPWM(3, 0, angleToPulse(125.5));delay(200); 
	    board3.setPWM(2, 0, angleToPulse(24));delay(200);
	  }
	  else if (number == 1) {
	    board2.setPWM(13, 0, angleToPulse(32));delay(200);
	    board2.setPWM(12, 0, angleToPulse(33));delay(200);
	    board2.setPWM(11, 0, angleToPulse(32));delay(200);
	    board2.setPWM(10, 0, angleToPulse(35));delay(200);
	    board2.setPWM(9, 0, angleToPulse(38));delay(200);
	    board2.setPWM(8, 0, angleToPulse(30));delay(200);
	    board2.setPWM(15, 0, angleToPulse(42));delay(200);
	    board2.setPWM(14, 0, angleToPulse(52));delay(200);
	    board3.setPWM(1, 0, angleToPulse(122));delay(200);
	    board3.setPWM(0, 0, angleToPulse(46));delay(200);
	    board3.setPWM(3, 0, angleToPulse(125));delay(200);
	    board3.setPWM(2, 0, angleToPulse(124));delay(200);
	  }
	  else if (number == 2) {
	    board2.setPWM(13, 0, angleToPulse(86));delay(200); 
	    board2.setPWM(12, 0, angleToPulse(90.5));delay(200);  
	    board2.setPWM(11, 0, angleToPulse(83));delay(200);
	    board2.setPWM(10, 0, angleToPulse(50));delay(200); 
	    board2.setPWM(9, 0, angleToPulse(124.5));delay(200); 
	    board2.setPWM(8, 0, angleToPulse(83.5));delay(200); 
	    board2.setPWM(15, 0, angleToPulse(43));delay(200); 
	    board2.setPWM(14, 0, angleToPulse(18));delay(200);
	    board3.setPWM(1, 0, angleToPulse(122));delay(200);
	    board3.setPWM(0, 0, angleToPulse(12));delay(200);
	    board3.setPWM(3, 0, angleToPulse(27));delay(200);
	    board3.setPWM(2, 0, angleToPulse(24));delay(200);
	  }
	  else if (number == 3) {
	    board2.setPWM(13, 0, angleToPulse(86));delay(200);
	    board2.setPWM(12, 0, angleToPulse(90));delay(200);
	    board2.setPWM(11, 0, angleToPulse(83));delay(200); 
	    board2.setPWM(10, 0, angleToPulse(87));delay(200);
	    board2.setPWM(9, 0, angleToPulse(91));delay(200);
	    board2.setPWM(8, 0, angleToPulse(84));delay(200); 
	    board2.setPWM(15, 0, angleToPulse(43));delay(200);
	    board2.setPWM(14, 0, angleToPulse(18));delay(200);
	    board3.setPWM(1, 0, angleToPulse(122));delay(200);
	    board3.setPWM(0, 0, angleToPulse(12));delay(200);
	    board3.setPWM(3, 0, angleToPulse(125));delay(200);
	    board3.setPWM(2, 0, angleToPulse(22));delay(200);
	  }
	  else if (number == 4) {
	    board2.setPWM(13, 0, angleToPulse(49));delay(200);
	    board2.setPWM(12, 0, angleToPulse(54));delay(200);
	    board2.setPWM(11, 0, angleToPulse(120));delay(200);
	    board2.setPWM(10, 0, angleToPulse(86));delay(200);
	    board2.setPWM(9, 0, angleToPulse(38));delay(200);
	    board2.setPWM(8, 0, angleToPulse(30));delay(200);
	    board2.setPWM(15, 0, angleToPulse(42));delay(200); 
	    board2.setPWM(14, 0, angleToPulse(52));delay(200);
	    board3.setPWM(1, 0, angleToPulse(122));delay(200);
	    board3.setPWM(0, 0, angleToPulse(47));delay(200); 
	    board3.setPWM(3, 0, angleToPulse(126));delay(200);
	    board3.setPWM(2, 0, angleToPulse(124));delay(200);  
	  }
	  else if (number == 5) {
	    board2.setPWM(13, 0, angleToPulse(86.5));delay(200); 
	    board2.setPWM(12, 0, angleToPulse(53));delay(200);
	    board2.setPWM(11, 0, angleToPulse(120));delay(200);
	    board2.setPWM(10, 0, angleToPulse(86));delay(200); 
	    board2.setPWM(9, 0, angleToPulse(90));delay(200);
	    board2.setPWM(8, 0, angleToPulse(85));delay(200);
	    board2.setPWM(15, 0, angleToPulse(8));delay(200);
	    board2.setPWM(14, 0, angleToPulse(21));delay(200);
	    board3.setPWM(1, 0, angleToPulse(49));delay(200); 
	    board3.setPWM(0, 0, angleToPulse(16));delay(200); 
	    board3.setPWM(3, 0, angleToPulse(125));delay(200);
	    board3.setPWM(2, 0, angleToPulse(24));delay(200);
	  }
	}
	
	/*4th digit*/
	
	void digit4(int number) {
	  if (number == 0) {
	    board3.setPWM(9, 0, angleToPulse(80));delay(200);
	    board3.setPWM(8, 0, angleToPulse(54));delay(200); 
	    board3.setPWM(7, 0, angleToPulse(116));delay(200);
	    board3.setPWM(6, 0, angleToPulse(54));delay(200); 
	    board3.setPWM(5, 0, angleToPulse(115));delay(200);
	    board3.setPWM(4, 0, angleToPulse(89));delay(200); 
	    board3.setPWM(15, 0, angleToPulse(20));delay(200);
	    board3.setPWM(14, 0, angleToPulse(53));delay(200); 
	    board3.setPWM(13, 0, angleToPulse(121));delay(200); 
	    board3.setPWM(12, 0, angleToPulse(56));delay(200);
	    board3.setPWM(11, 0, angleToPulse(117));delay(200); 
	    board3.setPWM(10, 0, angleToPulse(21));delay(200); 
	  }
	  else if (number == 1) {
	    board3.setPWM(9, 0, angleToPulse(28));delay(200);
	    board3.setPWM(8, 0, angleToPulse(36));delay(200);
	    board3.setPWM(7, 0, angleToPulse(36.5));delay(200); 
	    board3.setPWM(6, 0, angleToPulse(33.5));delay(200); 
	    board3.setPWM(5, 0, angleToPulse(32));delay(200);   
	    board3.setPWM(4, 0, angleToPulse(33));delay(200);
	    board3.setPWM(15, 0, angleToPulse(54));delay(200); 
	    board3.setPWM(14, 0, angleToPulse(52));delay(200); 
	    board3.setPWM(13, 0, angleToPulse(121));delay(200); 
	    board3.setPWM(12, 0, angleToPulse(56));delay(200); 
	    board3.setPWM(11, 0, angleToPulse(119));delay(200); 
	    board3.setPWM(10, 0, angleToPulse(120));delay(200); 
	  }
	  else if (number == 2) {
	    board3.setPWM(9, 0, angleToPulse(78));delay(200); 
	    board3.setPWM(8, 0, angleToPulse(88));delay(200);
	    board3.setPWM(7, 0, angleToPulse(82));delay(200); 
	    board3.setPWM(6, 0, angleToPulse(50));delay(200);
	    board3.setPWM(5, 0, angleToPulse(116));delay(200); 
	    board3.setPWM(4, 0, angleToPulse(88));delay(200); 
	    board3.setPWM(15, 0, angleToPulse(22));delay(200); 
	    board3.setPWM(14, 0, angleToPulse(54));delay(200);
	    board3.setPWM(13, 0, angleToPulse(122));delay(200); 
	    board3.setPWM(12, 0, angleToPulse(23));delay(200); 
	    board3.setPWM(11, 0, angleToPulse(20));delay(200); 
	    board3.setPWM(10, 0, angleToPulse(22));delay(200); 
	  }
	  else if (number == 3) {
	    board3.setPWM(9, 0, angleToPulse(78));delay(200);
	    board3.setPWM(8, 0, angleToPulse(88));delay(200); 
	    board3.setPWM(7, 0, angleToPulse(82));delay(200);
	    board3.setPWM(6, 0, angleToPulse(86));delay(200); 
	    board3.setPWM(5, 0, angleToPulse(85));delay(200);
	    board3.setPWM(4, 0, angleToPulse(88));delay(200);
	    board3.setPWM(15, 0, angleToPulse(22));delay(200); 
	    board3.setPWM(14, 0, angleToPulse(54));delay(200);
	    board3.setPWM(13, 0, angleToPulse(122));delay(200); 
	    board3.setPWM(12, 0, angleToPulse(23));delay(200); 
	    board3.setPWM(11, 0, angleToPulse(118));delay(200);
	    board3.setPWM(10, 0, angleToPulse(21));delay(200);
	  }
	  else if (number == 4) {
	    board3.setPWM(9, 0, angleToPulse(43));delay(200); 
	    board3.setPWM(8, 0, angleToPulse(56));delay(200);
	    board3.setPWM(7, 0, angleToPulse(116));delay(200); 
	    board3.setPWM(6, 0, angleToPulse(87));delay(200); 
	    board3.setPWM(5, 0, angleToPulse(32));delay(200);
	    board3.setPWM(4, 0, angleToPulse(33));delay(200);
	    board3.setPWM(15, 0, angleToPulse(54));delay(200); 
	    board3.setPWM(14, 0, angleToPulse(52));delay(200);
	    board3.setPWM(13, 0, angleToPulse(121));delay(200); 
	    board3.setPWM(12, 0, angleToPulse(56));delay(200); 
	    board3.setPWM(11, 0, angleToPulse(118));delay(200); 
	    board3.setPWM(10, 0, angleToPulse(119));delay(200); 
	  }
	  else if (number == 5) {
	    board3.setPWM(9, 0, angleToPulse(80));delay(200);
	    board3.setPWM(8, 0, angleToPulse(54));delay(200);
	    board3.setPWM(7, 0, angleToPulse(116));delay(200); 
	    board3.setPWM(6, 0, angleToPulse(87));delay(200); 
	    board3.setPWM(5, 0, angleToPulse(85));delay(200);
	    board3.setPWM(4, 0, angleToPulse(88));delay(200); 
	    board3.setPWM(15, 0, angleToPulse(21));delay(200);
	    board3.setPWM(14, 0, angleToPulse(21));delay(200); 
	    board3.setPWM(13, 0, angleToPulse(52));delay(200);
	    board3.setPWM(12, 0, angleToPulse(22));delay(200);
	    board3.setPWM(11, 0, angleToPulse(118));delay(200); 
	    board3.setPWM(10, 0, angleToPulse(22));delay(200);
	  }
	  else if (number == 6) {
	    board3.setPWM(9, 0, angleToPulse(80));delay(200);
	    board3.setPWM(8, 0, angleToPulse(54));delay(200);
	    board3.setPWM(7, 0, angleToPulse(116));delay(200);
	    board3.setPWM(6, 0, angleToPulse(54));delay(200); 
	    board3.setPWM(5, 0, angleToPulse(115));delay(200); 
	    board3.setPWM(4, 0, angleToPulse(89));delay(200); 
	    board3.setPWM(15, 0, angleToPulse(21));delay(200);
	    board3.setPWM(14, 0, angleToPulse(21));delay(200);
	    board3.setPWM(13, 0, angleToPulse(52));delay(200);
	    board3.setPWM(12, 0, angleToPulse(22));delay(200);
	    board3.setPWM(11, 0, angleToPulse(118));delay(200);
	    board3.setPWM(10, 0, angleToPulse(22));delay(200);
	  }
	  else if (number == 7) {
	    board3.setPWM(9, 0, angleToPulse(80));delay(200); 
	    board3.setPWM(8, 0, angleToPulse(87.5));delay(200);
	    board3.setPWM(7, 0, angleToPulse(36.5));delay(200); 
	    board3.setPWM(6, 0, angleToPulse(33.5));delay(200); 
	    board3.setPWM(5, 0, angleToPulse(32));delay(200); 
	    board3.setPWM(4, 0, angleToPulse(33));delay(200);
	    board3.setPWM(15, 0, angleToPulse(20));delay(200); 
	    board3.setPWM(14, 0, angleToPulse(53));delay(200); 
	    board3.setPWM(13, 0, angleToPulse(121));delay(200); 
	    board3.setPWM(12, 0, angleToPulse(57));delay(200); 
	    board3.setPWM(11, 0, angleToPulse(118));delay(200);
	    board3.setPWM(10, 0, angleToPulse(119));delay(200);
	  }
	  else if (number == 8) {
	    board3.setPWM(9, 0, angleToPulse(80));delay(200);
	    board3.setPWM(8, 0, angleToPulse(54));delay(200); 
	    board3.setPWM(7, 0, angleToPulse(116));delay(200); 
	    board3.setPWM(6, 0, angleToPulse(87));delay(200); 
	    board3.setPWM(5, 0, angleToPulse(117));delay(200);
	    board3.setPWM(4, 0, angleToPulse(88));delay(200); 
	    board3.setPWM(15, 0, angleToPulse(20));delay(200);
	    board3.setPWM(14, 0, angleToPulse(53));delay(200);
	    board3.setPWM(13, 0, angleToPulse(122));delay(200); 
	    board3.setPWM(12, 0, angleToPulse(23));delay(200); 
	    board3.setPWM(11, 0, angleToPulse(117));delay(200);
	    board3.setPWM(10, 0, angleToPulse(21));delay(200); 
	  }
	  else if (number == 9) {
	    board3.setPWM(9, 0, angleToPulse(80));delay(200);
	    board3.setPWM(8, 0, angleToPulse(54));delay(200); 
	    board3.setPWM(7, 0, angleToPulse(116));delay(200); 
	    board3.setPWM(6, 0, angleToPulse(87));delay(200); 
	    board3.setPWM(5, 0, angleToPulse(85));delay(200); 
	    board3.setPWM(4, 0, angleToPulse(88));delay(200);  
	    board3.setPWM(15, 0, angleToPulse(20));delay(200); 
	    board3.setPWM(14, 0, angleToPulse(53));delay(200); 
	    board3.setPWM(13, 0, angleToPulse(121));delay(200);
	    board3.setPWM(12, 0, angleToPulse(56));delay(200); 
	    board3.setPWM(11, 0, angleToPulse(117));delay(200); 
	    board3.setPWM(10, 0, angleToPulse(21));delay(200); 
	  }
	}

With the position of each clock hands calibrated, the clock could theorectically be used right away, however further fine adjustments to the servo motors were required to ensure the digits are as accurate as possible.

The code above is used to further calibrate the position of the hour and minute hands of the clocks to accurately display the desired digits. The process is explained below:

1. In the main void loop, the line - "digit2(number)" was changed between "1" to "4" based on which digit was being calibrated. 
2. For digits 2 and 4 of the clock, numbers "0" to "9" was required to be calibrated, while digit 1 only needed "0" to "2", and finally digit 3 needed "0" to "5".
3. For example, to calibrate the number "1" of the digit 1, the value of angle for the motors involved to make up that digit was changed slightly until the general shape of the number is as close to what a digital clock would display.
4. The process was repeated for all the remaining numbers and digits.

Before number cali After number cali

Here is a before (top) and after (bottom) picture of the calibration of the number six.

### Code

All the codes used in this project can be found [here](https://github.com/allen-michael-tan/Kinematic-clock/tree/main/code).

#### Real Time Clock (RTC) code

The RTC module used is called DS3231, the code is as of below. 

	#include <Wire.h>
	#include "RTClib.h"
	
	RTC_DS3231 rtc;
	
	char daysOfTheWeek[7][12] = {"Sunday", "Monday", "Tuesday", "Wednesday", "Thursday", "Friday", "Saturday"};
	
	void setup () 
	{
	  Serial.begin(9600);
	  
	  delay(3000); // wait for console opening
	
	  if (! rtc.begin()) {
	    Serial.println("Couldn't find RTC");
	    while (1);
	  }
	
	  if (rtc.lostPower()) {
	    Serial.println("RTC lost power, lets set the time!");
	  
	    // Comment out below lines once you set the date & time. Following line sets the RTC to the date & time this sketch was compiled
	    // rtc.adjust(DateTime(F(__DATE__), F(__TIME__)));
	  
	    // Following line sets the RTC with an explicit date & time, for example to set July 8 2021 at 13:30 you would call:
	    // rtc.adjust(DateTime(2021, 7, 8, 13, 30, 0));
	  }
	
	  // When time needs to be re-set on a previously configured device, the following line sets the RTC to the date & time this sketch was compiled
	  rtc.adjust(DateTime(F(__DATE__), F(__TIME__)));
	  // This line sets the RTC with an explicit date & time, for example to set July 8, 2021 at 13: you would call:
	  rtc.adjust(DateTime(2021, 7, 8, 13, 28, 0));
	}
	
	void printTime() {
	  
		DateTime now = rtc.now();
	    
	    Serial.print("Current Date & Time: ");
	    Serial.print(now.year(), DEC);
	    Serial.print('/');
	    Serial.print(now.month(), DEC);
	    Serial.print('/');
	    Serial.print(now.day(), DEC);
	    Serial.print(" (");
	    Serial.print(daysOfTheWeek[now.dayOfTheWeek()]);
	    Serial.print(") ");
	    Serial.print(now.hour(), DEC);
	    Serial.print(':');
	    Serial.print(now.minute(), DEC);
	    Serial.print(':');
	    Serial.print(now.second(), DEC);
	    Serial.println();
	    
	    delay(1000);
	}
	
	void loop () {
	    printTime();
	}

Before uploading the final code, this code was used to synchronise the time of the RTC to the current time. 

#### Full code

The code below is the final code used by the clock.

	#include <Wire.h>
	#include <Adafruit_PWMServoDriver.h>
	#include "RTClib.h"
	
	Adafruit_PWMServoDriver board1 = Adafruit_PWMServoDriver(0x40);
	Adafruit_PWMServoDriver board2 = Adafruit_PWMServoDriver(0x41);
	Adafruit_PWMServoDriver board3 = Adafruit_PWMServoDriver(0x42);
	
	#define SERVOMIN  544   // This is the 'minimum' pulse length count (out of 4096)
	#define SERVOMAX  2400  // This is the 'maximum' pulse length count (out of 4096)
	#define SERVO_FREQ 50   // Analog servos run at ~50 Hz updates
	
	RTC_DS3231 rtc;
	
	char daysOfTheWeek[7][12] = {"Sunday", "Monday", "Tuesday", "Wednesday", "Thursday", "Friday", "Saturday"};
	
	int hourPrevious;
	int hourCurrent;
	int minutePrevious;
	int minuteCurrent;
	
	int returndig1Previous;
	int returndig1Current;
	int returndig2;
	int returndig3Previous;
	int returndig3Current;
	int returndig4;
	
	void setup() {  
	  
	  Serial.begin(9600); 
	
	  /* Servo setup */
	
	  board1.begin();  // Initialize servo ccontrol boards
	  board2.begin();  
	  board3.begin();  
	  board1.setOscillatorFrequency(27000000);
	  board2.setOscillatorFrequency(27000000);
	  board3.setOscillatorFrequency(27000000);
	  board1.setPWMFreq(SERVO_FREQ);  // Analog servos run at ~50 Hz updates
	  board2.setPWMFreq(SERVO_FREQ); 
	  board3.setPWMFreq(SERVO_FREQ);
	  
	  yield();
	  
	  initialize();
	
	  /* RTC setup */
	
	  if (!rtc.begin()) {
	    Serial.println("Couldn't find RTC");
	    while (1);
	  }
	
	  if (rtc.lostPower()) {
	    Serial.println("RTC lost power, lets set the time!");
	  
	    // Comment out the two lines of code once the battery has been replaced and the date & time has been set.
	    // rtc.adjust(DateTime(F(__DATE__), F(__TIME__))); // Sets the RTC to the date & time this sketch was compiled
	    // rtc.adjust(DateTime(2021, 7, 1, 14, 30, 0));    // Sets the RTC with an explicit date & time, this line sets to July 1 2021, 13:51
	  }
	
	  // To reset the time on a previously configured device, reupload this code to the device with the comments removed, then comment them again to avoid any unnecessary rtc reset.
	  // rtc.adjust(DateTime(F(__DATE__), F(__TIME__)));
	  // rtc.adjust(DateTime(2021, 7, 1, 14, 30, 0));
	} 
	
	void loop() {  
	  
	  DateTime now = rtc.now();     // Get the time from RTC
	
	  hourCurrent = now.hour();     // The current hour (0 - 23)
	  minuteCurrent = now.minute(); // The current minute (0 - 59)
	
	  if (hourCurrent != hourPrevious) {               // Check if the hour has changed
	    returndig1Current = hourCurrent / 10;          // Get the 1st digit of the hour
	    returndig2 = hourCurrent % 10;                 // Get the 2nd digit of the hour
	    if (returndig1Current != returndig1Previous) { // Check to see if the first digit has changed (2nd digit will always change)
	      digit1(returndig1Current);                   // Change digit 1 on the clock to a new number
	      returndig1Previous = returndig1Current;      // Store the new number
	    }
	    digit2(returndig2);                            // Change digit 2 on the clock to a new number
	    hourPrevious = hourCurrent;                    // Store the new number
	  }
	
	  if (minuteCurrent != minutePrevious) {           // Check if the minute has changed
	    returndig3Current = minuteCurrent / 10;        // Get the 1st digit of the minute
	    returndig4 = minuteCurrent % 10;               // Get the 2nd digit of the minute
	    if (returndig3Current != returndig3Previous) { // Check to see if the first digit has changed (2nd digit will always change)
	      digit3(returndig3Current);                   // Change digit 3 on the clock to a new number
	      returndig3Previous = returndig3Current;      // Store the new number
	    }
	    digit4(returndig4);                            // Change digit 4 on the clock to a new number
	    minutePrevious = minuteCurrent;                // Store the new number
	  }
	
	  delay(15000);                                    // Wait 15s to check if time has changed
	}
	
	/* Determining the angles in which the servos move at */
	
	int angleToPulse(int ang){
	   int pulse1 = map(ang,0, 180, SERVOMIN,SERVOMAX); // Map the angles of 0 to 180 to Servo min and Servo max 
	   int pulse2 = int(float(pulse1) / 1000000 * SERVO_FREQ * 4096);
	   // Serial.print("Angle: ");Serial.print(ang);
	   // Serial.print(" pulse: ");Serial.println(pulse);
	   return pulse2;
	}
	
	/* Actual clock initialization */
	
	void initialize() {
	  DateTime now = rtc.now(); // Get the time from RTC
	
	  hourCurrent = (now.hour(), DEC);     // The current hour (0 - 23)
	  minuteCurrent = (now.minute(), DEC); // The current minute (0 - 59)
	
	  // Serial.print(hourCurrent); Serial.print(":"); Serial.println(minuteCurrent);
	  
	  returndig1Current = hourCurrent / 10;   // get 1st digit of hour
	  returndig2 = hourCurrent % 10;          // get 2nd digit of hour
	  returndig3Current = minuteCurrent / 10; // get 1st digit of minute
	  returndig4 = minuteCurrent % 10;        // get 2nd digit of minute
	  
	  // Serial.print(returndig1Current); Serial.print(returndig2); Serial.print(returndig3Current); Serial.println(returndig4);
	
	  for (int dig1 = 0; dig1 <= 2; dig1++){                 // Cycle 1st digit from 0-2
	    digit1(dig1);
	    // Serial.println(dig1);
	    delay(100);
	  }
	  for (int dig1 = 0; dig1 <= returndig1Current; dig1++){ // Cycle 1st digit from 0 to current time 
	    digit1(dig1);
	    // Serial.println(dig1);
	    delay(100);
	  }
	  
	  for (int dig2 = 0; dig2 <= 9; dig2++){                // Cycle 2nd digit from 0-9
	    digit2(dig2);
	    // Serial.println(dig2);
	    delay(100);
	  }
	  for (int dig2 = 0; dig2 <= returndig2; dig2++){       // Cycle 1st digit from 0 to current time
	    digit2(dig2);
	    // Serial.println(dig2);
	    delay(100);
	  }
	
	  for (int dig3 = 0; dig3 <= 5; dig3++){                 // Cycle 3rd digit from 0-5
	    digit3(dig3);
	    delay(100);
	  }
	  for (int dig3 = 0; dig3 <= returndig3Current; dig3++){ // Cycle 1st digit from 0 to current time
	    digit3(dig3);
	    delay(100);
	  }
	
	  for (int dig4 = 0; dig4 <= 9; dig4++){                // Cycle 4th digit from 0-9
	    digit4(dig4);
	    delay(100);
	  }
	  for (int dig4 = 0; dig4 <= returndig4; dig4++){       // Cycle 1st digit from 0 to current time
	    digit4(dig4);
	    delay(100);
	  }
	}
	
	/*The code below are found in the Kinematic clock calibration excel file, under the sheet named "Calibrated digits"
	
	/*1st digit*/
	
	void digit1(int number) {
	  if (number == 0) {
	    board1.setPWM(5, 0, angleToPulse(72));delay(200);
	    board1.setPWM(4, 0, angleToPulse(40));delay(200); 
	    board1.setPWM(3, 0, angleToPulse(116));delay(200);
	    board1.setPWM(2, 0, angleToPulse(40));delay(200);
	    board1.setPWM(1, 0, angleToPulse(119));delay(200);
	    board1.setPWM(0, 0, angleToPulse(88));delay(200);
	    board1.setPWM(11, 0, angleToPulse(53));delay(200);
	    board1.setPWM(10, 0, angleToPulse(8));delay(200);
	    board1.setPWM(9, 0, angleToPulse(110));delay(200);
	    board1.setPWM(8, 0, angleToPulse(38));delay(200);
	    board1.setPWM(7, 0, angleToPulse(120));delay(200);
	    board1.setPWM(6, 0, angleToPulse(16));delay(200);
	  }
	  else if (number == 1) {
	    board1.setPWM(5, 0, angleToPulse(16));delay(200);
	    board1.setPWM(4, 0, angleToPulse(19));delay(200);
	    board1.setPWM(3, 0, angleToPulse(20));delay(200);
	    board1.setPWM(2, 0, angleToPulse(19));delay(200);
	    board1.setPWM(1, 0, angleToPulse(19));delay(200);
	    board1.setPWM(0, 0, angleToPulse(30));delay(200);
	    board1.setPWM(11, 0, angleToPulse(52));delay(200);
	    board1.setPWM(10, 0, angleToPulse(41));delay(200);
	    board1.setPWM(9, 0, angleToPulse(110));delay(200);
	    board1.setPWM(8, 0, angleToPulse(38));delay(200);
	    board1.setPWM(7, 0, angleToPulse(120));delay(200);
	    board1.setPWM(6, 0, angleToPulse(125));delay(200);
	  }
	  else if (number == 2) {
	    board1.setPWM(5, 0, angleToPulse(73));delay(200); 
	    board1.setPWM(4, 0, angleToPulse(76));delay(200);
	    board1.setPWM(3, 0, angleToPulse(79));delay(200);
	    board1.setPWM(2, 0, angleToPulse(39));delay(200);
	    board1.setPWM(1, 0, angleToPulse(119));delay(200);
	    board1.setPWM(0, 0, angleToPulse(88));delay(200);
	    board1.setPWM(11, 0, angleToPulse(53));delay(200); 
	    board1.setPWM(10, 0, angleToPulse(8));delay(200);
	    board1.setPWM(9, 0, angleToPulse(112));delay(200);
	    board1.setPWM(8, 0, angleToPulse(1));delay(200);
	    board1.setPWM(7, 0, angleToPulse(15));delay(200);
	    board1.setPWM(6, 0, angleToPulse(16));delay(200);
	  }
	}
	
	/*2nd digit*/
	
	void digit2(int number) {
	  if (number == 0) {
	    board2.setPWM(1, 0, angleToPulse(88));delay(200); 
	    board2.setPWM(0, 0, angleToPulse(46));delay(200); 
	    board1.setPWM(15, 0, angleToPulse(120));delay(200); 
	    board1.setPWM(14, 0, angleToPulse(45));delay(200); 
	    board1.setPWM(13, 0, angleToPulse(119));delay(200); 
	    board1.setPWM(12, 0, angleToPulse(78));delay(200);
	    board2.setPWM(7, 0, angleToPulse(44));delay(200);
	    board2.setPWM(6, 0, angleToPulse(6));delay(200);
	    board2.setPWM(5, 0, angleToPulse(122));delay(200); 
	    board2.setPWM(4, 0, angleToPulse(46));delay(200);
	    board2.setPWM(3, 0, angleToPulse(124));delay(200);
	    board2.setPWM(2, 0, angleToPulse(14));delay(200);
	  }
	  else if (number == 1) {
	    board2.setPWM(1, 0, angleToPulse(33));delay(200);
	    board2.setPWM(0, 0, angleToPulse(29));delay(200);
	    board1.setPWM(15, 0, angleToPulse(25));delay(200);
	    board1.setPWM(14, 0, angleToPulse(26));delay(200); 
	    board1.setPWM(13, 0, angleToPulse(27));delay(200);
	    board1.setPWM(12, 0, angleToPulse(21));delay(200); 
	    board2.setPWM(7, 0, angleToPulse(44));delay(200);  
	    board2.setPWM(6, 0, angleToPulse(37));delay(200); 
	    board2.setPWM(5, 0, angleToPulse(122));delay(200); 
	    board2.setPWM(4, 0, angleToPulse(46));delay(200); 
	    board2.setPWM(3, 0, angleToPulse(125));delay(200); 
	    board2.setPWM(2, 0, angleToPulse(120));delay(200);
	  }
	  else if (number == 2) {
	    board2.setPWM(1, 0, angleToPulse(87));delay(200); 
	    board2.setPWM(0, 0, angleToPulse(79));delay(200); 
	    board1.setPWM(15, 0, angleToPulse(81));delay(200);
	    board1.setPWM(14, 0, angleToPulse(44));delay(200); 
	    board1.setPWM(13, 0, angleToPulse(119));delay(200); 
	    board1.setPWM(12, 0, angleToPulse(83));delay(200); 
	    board2.setPWM(7, 0, angleToPulse(44));delay(200);
	    board2.setPWM(6, 0, angleToPulse(7));delay(200);
	    board2.setPWM(5, 0, angleToPulse(122));delay(200);
	    board2.setPWM(4, 0, angleToPulse(11));delay(200);
	    board2.setPWM(3, 0, angleToPulse(18));delay(200); 
	    board2.setPWM(2, 0, angleToPulse(14));delay(200);
	  }
	  else if (number == 3) {
	    board2.setPWM(1, 0, angleToPulse(87));delay(200);
	    board2.setPWM(0, 0, angleToPulse(79));delay(200);
	    board1.setPWM(15, 0, angleToPulse(82));delay(200); 
	    board1.setPWM(14, 0, angleToPulse(79));delay(200);
	    board1.setPWM(13, 0, angleToPulse(79));delay(200); 
	    board1.setPWM(12, 0, angleToPulse(84));delay(200); 
	    board2.setPWM(7, 0, angleToPulse(44));delay(200); 
	    board2.setPWM(6, 0, angleToPulse(7));delay(200);  
	    board2.setPWM(5, 0, angleToPulse(122));delay(200); 
	    board2.setPWM(4, 0, angleToPulse(11));delay(200); 
	    board2.setPWM(3, 0, angleToPulse(124));delay(200);
	    board2.setPWM(2, 0, angleToPulse(13));delay(200); 
	  }
	  else if (number == 4) {
	    board2.setPWM(1, 0, angleToPulse(53));delay(200);
	    board2.setPWM(0, 0, angleToPulse(47));delay(200);
	    board1.setPWM(15, 0, angleToPulse(119));delay(200); 
	    board1.setPWM(14, 0, angleToPulse(79));delay(200);
	    board1.setPWM(13, 0, angleToPulse(27));delay(200);
	    board1.setPWM(12, 0, angleToPulse(20));delay(200);
	    board2.setPWM(7, 0, angleToPulse(44));delay(200); 
	    board2.setPWM(6, 0, angleToPulse(37));delay(200); 
	    board2.setPWM(5, 0, angleToPulse(122));delay(200);
	    board2.setPWM(4, 0, angleToPulse(45));delay(200); 
	    board2.setPWM(3, 0, angleToPulse(125));delay(200); 
	    board2.setPWM(2, 0, angleToPulse(120));delay(200);
	  }
	  else if (number == 5) {
	    board2.setPWM(1, 0, angleToPulse(88));delay(200); 
	    board2.setPWM(0, 0, angleToPulse(45));delay(200); 
	    board1.setPWM(15, 0, angleToPulse(119));delay(200); 
	    board1.setPWM(14, 0, angleToPulse(80));delay(200); 
	    board1.setPWM(13, 0, angleToPulse(78));delay(200);
	    board1.setPWM(12, 0, angleToPulse(82));delay(200); 
	    board2.setPWM(7, 0, angleToPulse(12));delay(200);
	    board2.setPWM(6, 0, angleToPulse(7));delay(200);
	    board2.setPWM(5, 0, angleToPulse(49));delay(200); 
	    board2.setPWM(4, 0, angleToPulse(11));delay(200); 
	    board2.setPWM(3, 0, angleToPulse(124));delay(200); 
	    board2.setPWM(2, 0, angleToPulse(14));delay(200); 
	  }
	  else if (number == 6) {
	    board2.setPWM(1, 0, angleToPulse(88));delay(200);
	    board2.setPWM(0, 0, angleToPulse(45));delay(200);
	    board1.setPWM(15, 0, angleToPulse(120));delay(200);
	    board1.setPWM(14, 0, angleToPulse(44));delay(200); 
	    board1.setPWM(13, 0, angleToPulse(120));delay(200); 
	    board1.setPWM(12, 0, angleToPulse(78));delay(200);
	    board2.setPWM(7, 0, angleToPulse(12));delay(200);
	    board2.setPWM(6, 0, angleToPulse(7));delay(200);
	    board2.setPWM(5, 0, angleToPulse(49));delay(200); 
	    board2.setPWM(4, 0, angleToPulse(11));delay(200);
	    board2.setPWM(3, 0, angleToPulse(124));delay(200);
	    board2.setPWM(2, 0, angleToPulse(14));delay(200); 
	  }
	  else if (number == 7) {
	    board2.setPWM(1, 0, angleToPulse(87));delay(200);
	    board2.setPWM(0, 0, angleToPulse(79));delay(200);
	    board1.setPWM(15, 0, angleToPulse(25));delay(200);
	    board1.setPWM(14, 0, angleToPulse(26));delay(200);
	    board1.setPWM(13, 0, angleToPulse(27));delay(200);
	    board1.setPWM(12, 0, angleToPulse(21));delay(200);
	    board2.setPWM(7, 0, angleToPulse(43));delay(200);
	    board2.setPWM(6, 0, angleToPulse(6));delay(200); 
	    board2.setPWM(5, 0, angleToPulse(122));delay(200);
	    board2.setPWM(4, 0, angleToPulse(45));delay(200); 
	    board2.setPWM(3, 0, angleToPulse(125));delay(200);
	    board2.setPWM(2, 0, angleToPulse(120));delay(200);
	  }
	  else if (number == 8) {
	    board2.setPWM(1, 0, angleToPulse(88));delay(200);
	    board2.setPWM(0, 0, angleToPulse(46));delay(200);
	    board1.setPWM(15, 0, angleToPulse(120));delay(200);
	    board1.setPWM(14, 0, angleToPulse(80));delay(200); 
	    board1.setPWM(13, 0, angleToPulse(119));delay(200); 
	    board1.setPWM(12, 0, angleToPulse(83));delay(200);
	    board2.setPWM(7, 0, angleToPulse(44));delay(200); 
	    board2.setPWM(6, 0, angleToPulse(6));delay(200); 
	    board2.setPWM(5, 0, angleToPulse(122));delay(200); 
	    board2.setPWM(4, 0, angleToPulse(11));delay(200);
	    board2.setPWM(3, 0, angleToPulse(124));delay(200);
	    board2.setPWM(2, 0, angleToPulse(14));delay(200);
	  }
	  else if (number == 9) {
	    board2.setPWM(1, 0, angleToPulse(88));delay(200); 
	    board2.setPWM(0, 0, angleToPulse(46));delay(200);
	    board1.setPWM(15, 0, angleToPulse(120));delay(200);
	    board1.setPWM(14, 0, angleToPulse(80));delay(200);
	    board1.setPWM(13, 0, angleToPulse(79));delay(200); 
	    board1.setPWM(12, 0, angleToPulse(84));delay(200);
	    board2.setPWM(7, 0, angleToPulse(44));delay(200);
	    board2.setPWM(6, 0, angleToPulse(6));delay(200);
	    board2.setPWM(5, 0, angleToPulse(122));delay(200); 
	    board2.setPWM(4, 0, angleToPulse(45));delay(200); 
	    board2.setPWM(3, 0, angleToPulse(124));delay(200);
	    board2.setPWM(2, 0, angleToPulse(14));delay(200);
	  }
	}
	
	/*3rd digit*/
	
	void digit3(int number) {
	  if (number == 0) {
	    board2.setPWM(13, 0, angleToPulse(86.5));delay(200);
	    board2.setPWM(12, 0, angleToPulse(53));delay(200);
	    board2.setPWM(11, 0, angleToPulse(120));delay(200);
	    board2.setPWM(10, 0, angleToPulse(52));delay(200);
	    board2.setPWM(9, 0, angleToPulse(124));delay(200);
	    board2.setPWM(8, 0, angleToPulse(85));delay(200);
	    board2.setPWM(15, 0, angleToPulse(43));delay(200);
	    board2.setPWM(14, 0, angleToPulse(18));delay(200); 
	    board3.setPWM(1, 0, angleToPulse(122));delay(200);
	    board3.setPWM(0, 0, angleToPulse(46));delay(200);
	    board3.setPWM(3, 0, angleToPulse(125.5));delay(200); 
	    board3.setPWM(2, 0, angleToPulse(24));delay(200);
	  }
	  else if (number == 1) {
	    board2.setPWM(13, 0, angleToPulse(32));delay(200);
	    board2.setPWM(12, 0, angleToPulse(33));delay(200);
	    board2.setPWM(11, 0, angleToPulse(32));delay(200);
	    board2.setPWM(10, 0, angleToPulse(35));delay(200);
	    board2.setPWM(9, 0, angleToPulse(38));delay(200);
	    board2.setPWM(8, 0, angleToPulse(30));delay(200);
	    board2.setPWM(15, 0, angleToPulse(42));delay(200);
	    board2.setPWM(14, 0, angleToPulse(52));delay(200);
	    board3.setPWM(1, 0, angleToPulse(122));delay(200);
	    board3.setPWM(0, 0, angleToPulse(46));delay(200);
	    board3.setPWM(3, 0, angleToPulse(125));delay(200);
	    board3.setPWM(2, 0, angleToPulse(124));delay(200);
	  }
	  else if (number == 2) {
	    board2.setPWM(13, 0, angleToPulse(86));delay(200); 
	    board2.setPWM(12, 0, angleToPulse(90.5));delay(200);  
	    board2.setPWM(11, 0, angleToPulse(83));delay(200);
	    board2.setPWM(10, 0, angleToPulse(50));delay(200); 
	    board2.setPWM(9, 0, angleToPulse(124.5));delay(200); 
	    board2.setPWM(8, 0, angleToPulse(83.5));delay(200); 
	    board2.setPWM(15, 0, angleToPulse(43));delay(200); 
	    board2.setPWM(14, 0, angleToPulse(18));delay(200);
	    board3.setPWM(1, 0, angleToPulse(122));delay(200);
	    board3.setPWM(0, 0, angleToPulse(12));delay(200);
	    board3.setPWM(3, 0, angleToPulse(27));delay(200);
	    board3.setPWM(2, 0, angleToPulse(24));delay(200);
	  }
	  else if (number == 3) {
	    board2.setPWM(13, 0, angleToPulse(86));delay(200);
	    board2.setPWM(12, 0, angleToPulse(90));delay(200);
	    board2.setPWM(11, 0, angleToPulse(83));delay(200); 
	    board2.setPWM(10, 0, angleToPulse(87));delay(200);
	    board2.setPWM(9, 0, angleToPulse(91));delay(200);
	    board2.setPWM(8, 0, angleToPulse(84));delay(200); 
	    board2.setPWM(15, 0, angleToPulse(43));delay(200);
	    board2.setPWM(14, 0, angleToPulse(18));delay(200);
	    board3.setPWM(1, 0, angleToPulse(122));delay(200);
	    board3.setPWM(0, 0, angleToPulse(12));delay(200);
	    board3.setPWM(3, 0, angleToPulse(125));delay(200);
	    board3.setPWM(2, 0, angleToPulse(22));delay(200);
	  }
	  else if (number == 4) {
	    board2.setPWM(13, 0, angleToPulse(49));delay(200);
	    board2.setPWM(12, 0, angleToPulse(54));delay(200);
	    board2.setPWM(11, 0, angleToPulse(120));delay(200);
	    board2.setPWM(10, 0, angleToPulse(86));delay(200);
	    board2.setPWM(9, 0, angleToPulse(38));delay(200);
	    board2.setPWM(8, 0, angleToPulse(30));delay(200);
	    board2.setPWM(15, 0, angleToPulse(42));delay(200); 
	    board2.setPWM(14, 0, angleToPulse(52));delay(200);
	    board3.setPWM(1, 0, angleToPulse(122));delay(200);
	    board3.setPWM(0, 0, angleToPulse(47));delay(200); 
	    board3.setPWM(3, 0, angleToPulse(126));delay(200);
	    board3.setPWM(2, 0, angleToPulse(124));delay(200);  
	  }
	  else if (number == 5) {
	    board2.setPWM(13, 0, angleToPulse(86.5));delay(200); 
	    board2.setPWM(12, 0, angleToPulse(53));delay(200);
	    board2.setPWM(11, 0, angleToPulse(120));delay(200);
	    board2.setPWM(10, 0, angleToPulse(86));delay(200); 
	    board2.setPWM(9, 0, angleToPulse(90));delay(200);
	    board2.setPWM(8, 0, angleToPulse(85));delay(200);
	    board2.setPWM(15, 0, angleToPulse(8));delay(200);
	    board2.setPWM(14, 0, angleToPulse(21));delay(200);
	    board3.setPWM(1, 0, angleToPulse(49));delay(200); 
	    board3.setPWM(0, 0, angleToPulse(16));delay(200); 
	    board3.setPWM(3, 0, angleToPulse(125));delay(200);
	    board3.setPWM(2, 0, angleToPulse(24));delay(200);
	  }
	}
	
	/*4th digit*/
	
	void digit4(int number) {
	  if (number == 0) {
	    board3.setPWM(9, 0, angleToPulse(80));delay(200);
	    board3.setPWM(8, 0, angleToPulse(54));delay(200); 
	    board3.setPWM(7, 0, angleToPulse(116));delay(200);
	    board3.setPWM(6, 0, angleToPulse(54));delay(200); 
	    board3.setPWM(5, 0, angleToPulse(115));delay(200);
	    board3.setPWM(4, 0, angleToPulse(89));delay(200); 
	    board3.setPWM(15, 0, angleToPulse(20));delay(200);
	    board3.setPWM(14, 0, angleToPulse(53));delay(200); 
	    board3.setPWM(13, 0, angleToPulse(121));delay(200); 
	    board3.setPWM(12, 0, angleToPulse(56));delay(200);
	    board3.setPWM(11, 0, angleToPulse(117));delay(200); 
	    board3.setPWM(10, 0, angleToPulse(21));delay(200); 
	  }
	  else if (number == 1) {
	    board3.setPWM(9, 0, angleToPulse(28));delay(200);
	    board3.setPWM(8, 0, angleToPulse(36));delay(200);
	    board3.setPWM(7, 0, angleToPulse(36.5));delay(200); 
	    board3.setPWM(6, 0, angleToPulse(33.5));delay(200); 
	    board3.setPWM(5, 0, angleToPulse(32));delay(200);   
	    board3.setPWM(4, 0, angleToPulse(33));delay(200);
	    board3.setPWM(15, 0, angleToPulse(54));delay(200); 
	    board3.setPWM(14, 0, angleToPulse(52));delay(200); 
	    board3.setPWM(13, 0, angleToPulse(121));delay(200); 
	    board3.setPWM(12, 0, angleToPulse(56));delay(200); 
	    board3.setPWM(11, 0, angleToPulse(119));delay(200); 
	    board3.setPWM(10, 0, angleToPulse(120));delay(200); 
	  }
	  else if (number == 2) {
	    board3.setPWM(9, 0, angleToPulse(78));delay(200); 
	    board3.setPWM(8, 0, angleToPulse(88));delay(200);
	    board3.setPWM(7, 0, angleToPulse(82));delay(200); 
	    board3.setPWM(6, 0, angleToPulse(50));delay(200);
	    board3.setPWM(5, 0, angleToPulse(116));delay(200); 
	    board3.setPWM(4, 0, angleToPulse(88));delay(200); 
	    board3.setPWM(15, 0, angleToPulse(22));delay(200); 
	    board3.setPWM(14, 0, angleToPulse(54));delay(200);
	    board3.setPWM(13, 0, angleToPulse(122));delay(200); 
	    board3.setPWM(12, 0, angleToPulse(23));delay(200); 
	    board3.setPWM(11, 0, angleToPulse(20));delay(200); 
	    board3.setPWM(10, 0, angleToPulse(22));delay(200); 
	  }
	  else if (number == 3) {
	    board3.setPWM(9, 0, angleToPulse(78));delay(200);
	    board3.setPWM(8, 0, angleToPulse(88));delay(200); 
	    board3.setPWM(7, 0, angleToPulse(82));delay(200);
	    board3.setPWM(6, 0, angleToPulse(86));delay(200); 
	    board3.setPWM(5, 0, angleToPulse(85));delay(200);
	    board3.setPWM(4, 0, angleToPulse(88));delay(200);
	    board3.setPWM(15, 0, angleToPulse(22));delay(200); 
	    board3.setPWM(14, 0, angleToPulse(54));delay(200);
	    board3.setPWM(13, 0, angleToPulse(122));delay(200); 
	    board3.setPWM(12, 0, angleToPulse(23));delay(200); 
	    board3.setPWM(11, 0, angleToPulse(118));delay(200);
	    board3.setPWM(10, 0, angleToPulse(21));delay(200);
	  }
	  else if (number == 4) {
	    board3.setPWM(9, 0, angleToPulse(43));delay(200); 
	    board3.setPWM(8, 0, angleToPulse(56));delay(200);
	    board3.setPWM(7, 0, angleToPulse(116));delay(200); 
	    board3.setPWM(6, 0, angleToPulse(87));delay(200); 
	    board3.setPWM(5, 0, angleToPulse(32));delay(200);
	    board3.setPWM(4, 0, angleToPulse(33));delay(200);
	    board3.setPWM(15, 0, angleToPulse(54));delay(200); 
	    board3.setPWM(14, 0, angleToPulse(52));delay(200);
	    board3.setPWM(13, 0, angleToPulse(121));delay(200); 
	    board3.setPWM(12, 0, angleToPulse(56));delay(200); 
	    board3.setPWM(11, 0, angleToPulse(118));delay(200); 
	    board3.setPWM(10, 0, angleToPulse(119));delay(200); 
	  }
	  else if (number == 5) {
	    board3.setPWM(9, 0, angleToPulse(80));delay(200);
	    board3.setPWM(8, 0, angleToPulse(54));delay(200);
	    board3.setPWM(7, 0, angleToPulse(116));delay(200); 
	    board3.setPWM(6, 0, angleToPulse(87));delay(200); 
	    board3.setPWM(5, 0, angleToPulse(85));delay(200);
	    board3.setPWM(4, 0, angleToPulse(88));delay(200); 
	    board3.setPWM(15, 0, angleToPulse(21));delay(200);
	    board3.setPWM(14, 0, angleToPulse(21));delay(200); 
	    board3.setPWM(13, 0, angleToPulse(52));delay(200);
	    board3.setPWM(12, 0, angleToPulse(22));delay(200);
	    board3.setPWM(11, 0, angleToPulse(118));delay(200); 
	    board3.setPWM(10, 0, angleToPulse(22));delay(200);
	  }
	  else if (number == 6) {
	    board3.setPWM(9, 0, angleToPulse(80));delay(200);
	    board3.setPWM(8, 0, angleToPulse(54));delay(200);
	    board3.setPWM(7, 0, angleToPulse(116));delay(200);
	    board3.setPWM(6, 0, angleToPulse(54));delay(200); 
	    board3.setPWM(5, 0, angleToPulse(115));delay(200); 
	    board3.setPWM(4, 0, angleToPulse(89));delay(200); 
	    board3.setPWM(15, 0, angleToPulse(21));delay(200);
	    board3.setPWM(14, 0, angleToPulse(21));delay(200);
	    board3.setPWM(13, 0, angleToPulse(52));delay(200);
	    board3.setPWM(12, 0, angleToPulse(22));delay(200);
	    board3.setPWM(11, 0, angleToPulse(118));delay(200);
	    board3.setPWM(10, 0, angleToPulse(22));delay(200);
	  }
	  else if (number == 7) {
	    board3.setPWM(9, 0, angleToPulse(80));delay(200); 
	    board3.setPWM(8, 0, angleToPulse(87.5));delay(200);
	    board3.setPWM(7, 0, angleToPulse(36.5));delay(200); 
	    board3.setPWM(6, 0, angleToPulse(33.5));delay(200); 
	    board3.setPWM(5, 0, angleToPulse(32));delay(200); 
	    board3.setPWM(4, 0, angleToPulse(33));delay(200);
	    board3.setPWM(15, 0, angleToPulse(20));delay(200); 
	    board3.setPWM(14, 0, angleToPulse(53));delay(200); 
	    board3.setPWM(13, 0, angleToPulse(121));delay(200); 
	    board3.setPWM(12, 0, angleToPulse(57));delay(200); 
	    board3.setPWM(11, 0, angleToPulse(118));delay(200);
	    board3.setPWM(10, 0, angleToPulse(119));delay(200);
	  }
	  else if (number == 8) {
	    board3.setPWM(9, 0, angleToPulse(80));delay(200);
	    board3.setPWM(8, 0, angleToPulse(54));delay(200); 
	    board3.setPWM(7, 0, angleToPulse(116));delay(200); 
	    board3.setPWM(6, 0, angleToPulse(87));delay(200); 
	    board3.setPWM(5, 0, angleToPulse(117));delay(200);
	    board3.setPWM(4, 0, angleToPulse(88));delay(200); 
	    board3.setPWM(15, 0, angleToPulse(20));delay(200);
	    board3.setPWM(14, 0, angleToPulse(53));delay(200);
	    board3.setPWM(13, 0, angleToPulse(122));delay(200); 
	    board3.setPWM(12, 0, angleToPulse(23));delay(200); 
	    board3.setPWM(11, 0, angleToPulse(117));delay(200);
	    board3.setPWM(10, 0, angleToPulse(21));delay(200); 
	  }
	  else if (number == 9) {
	    board3.setPWM(9, 0, angleToPulse(80));delay(200);
	    board3.setPWM(8, 0, angleToPulse(54));delay(200); 
	    board3.setPWM(7, 0, angleToPulse(116));delay(200); 
	    board3.setPWM(6, 0, angleToPulse(87));delay(200); 
	    board3.setPWM(5, 0, angleToPulse(85));delay(200); 
	    board3.setPWM(4, 0, angleToPulse(88));delay(200);  
	    board3.setPWM(15, 0, angleToPulse(20));delay(200); 
	    board3.setPWM(14, 0, angleToPulse(53));delay(200); 
	    board3.setPWM(13, 0, angleToPulse(121));delay(200);
	    board3.setPWM(12, 0, angleToPulse(56));delay(200); 
	    board3.setPWM(11, 0, angleToPulse(117));delay(200); 
	    board3.setPWM(10, 0, angleToPulse(21));delay(200); 
	  }
	}

## Final Product

Once the full code has been uploaded, the board was mounted onto the wall and plugged into the wall. 

Final product

Here is a timelapse of the clock in action!

Timelapse video (https://youtu.be/6yjyvjCh0M8)

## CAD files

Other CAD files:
Inventor files/Board.ipt
Inventor files/Breadth Board.ipt
Inventor files/Clock body v2.ipt
Inventor files/Clock sub-assembly.iam
Inventor files/Hour hand gear.ipt
Inventor files/Hour hand stopper.ipt
Inventor files/Hour hand.ipt
Inventor files/Hour shaft.ipt
Inventor files/Length Board.ipt
Inventor files/Minute hand gear.ipt
Inventor files/Minute hand shaft.ipt
Inventor files/Minute hand.ipt
Inventor files/Servo gear.ipt
Inventor files/Servo motor.ipt

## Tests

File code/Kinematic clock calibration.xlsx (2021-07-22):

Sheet: Calibration Table
Clock Calibration Table
 |  | 1 |  |  |  | 2 |  |  |  | 3 |  |  |  | 4 |  |  |  | 5 |  |  |  | 6 |  |  |  | 7 |  |  |  | 8
 |  | Hour |  | Minute |  | Hour |  | Minute |  | Hour |  | Minute |  | Hour |  | Minute |  | Hour |  | Minute |  | Hour |  | Minute |  | Hour |  | Minute |  | Hour |  | Minute
Position |  | CW | CCW | CW | CCW | CW | CCW | CW | CCW | CW | CCW | CW | CCW | CW | CCW | CW | CCW | CW | CCW | CW | CCW | CW | CCW | CW | CCW | CW | CCW | CW | CCW | CW | CCW | CW | CCW
A | 12
 | 3 | 73 | 73 | 77 | 77 |  |  |  |  | 88 | 88 | 80 | 81 |  |  |  |  | 83 | 84 | 85 | 90 |  |  |  |  | 78 | 78 | 86 | 86
 | 6 | 35 | 35 | 39 | 42 | 53 | 50 |  | 43 | 51 | 50 | 48 | 47 |  | 45 |  | 37 | 50 | 46 | 55 | 54 |  | 45 |  | 53 | 43 | 43 | 53 | 51 |  | 56 |  | 52
 | 7.5 | 19 |  | 23 |  |  |  |  |  | 35 |  | 32 |  |  |  |  |  | 32 |  | 37 |  |  |  |  |  | 28 |  | 38
 | 9 | 3 |  | 6 |  | 16 |  | 8 |  | 18 |  | 15 |  | 13 |  | 5 |  | 13 |  | 18 |  | 8 |  | 20 |  | 12 |  | 23 |  | 30 |  | 19
B | 12 |  | 117 |  | 112 |  | 112 |  | 116 |  | 120 |  | 117 |  | 123 |  | 118 |  | 120 |  | 122 |  | 123 |  | 118 |  | 117 |  | 119 |  | 123 |  | 122
 | 3 | 79 | 77 | 73 | 76 |  |  |  |  | 84 | 83 | 79 | 79 |  |  |  |  | 85 | 83 | 87 | 87 |  |  |  |  | 95 | 83 | 87 | 87
 | 6 | 41 | 40 | 40 | 40 | 37 | 36 | 37 | 39 | 45 | 48 | 45 | 45 | 51 | 49 | 50 | 49 | 48 | 46 | 52 | 50 | 50 | 50 | 45 | 48 | 55 | 51 | 53 | 50 | 53 | 57 | 54 | 57
 | 7.5 | 24 |  | 24 |  |  |  |  |  | 29 |  | 28 |  |  |  |  |  | 32 |  | 35 |  |  |  |  |  | 42 |  | 37
 | 9 | 6 |  | 7 |  | 5 |  | 2 |  | 12 |  | 10 |  | 18 |  | 13 |  | 15 |  | 17 |  | 19 |  | 15 |  | 28 |  | 20 |  | 23 |  | 24
C | 12 |  | 118 |  | 126 |  | 119 |  | 128 |  | 120 |  | 122 |  | 125 |  | 120 |  | 125 |  | 122 |  | 125 |  | 123 |  | 118 |  | 120 |  | 118 |  | 119
 | 3 | 83 | 81 | 90 | 85 |  |  |  |  | 79 | 77 | 80 | 83 |  |  |  |  | 88 | 92 | 84 | 85 |  |  |  |  | 85 | 85 | 90 | 90
 | 6 | 43 | 41 | 45 | 47 |  |  |  |  | 42 | 42 | 43 | 40 |  |  |  |  | 54 | 55 | 45 | 48 |  |  |  |  | 50 | 50 | 55 | 55
 | 7.5 | 25 |  | 29 |  |  |  |  |  | 27 |  | 27 |  |  |  |  |  | 39 |  | 30 |  |  |  |  |  | 34 |  | 39
 | 9 | 7 |  | 12 |  | 12 |  | 15 |  | 11 |  | 10 |  | 16 |  | 14 |  | 24 |  | 14 |  | 27 |  | 25 |  | 17 |  | 22 |  | 21 |  | 23
 | 7.5 is a calculated value from 3 & 6
Values for Lookup formula from table above.
No need to edit. Values are linked to table.
A1H7CW | 19
A1M7CW | 23
B1H7CW | 24
B1M7CW | 24
C1H7CW | 25
C1M7CW | 29
A3H7CW | 35
A3M7CW | 32
B3H7CW | 29
B3M7CW | 28
C3H7CW | 27
C3M7CW | 27
A5H7CW | 32
A5M7CW | 37
B5H7CW | 32
B5M7CW | 35
C5H7CW | 39
C5M7CW | 30
A7H7CW | 28
A7M7CW | 38
B7H7CW | 42
B7M7CW | 37
C7H7CW | 34
C7M7CW | 39
A1H3CW | 73
A1H3CCW | 73
A1H6CW | 35
A1H6CCW | 35
A1H9CW | 3
B1H12CCW | 117
B1H3CW | 79
B1H3CCW | 77
B1H6CW | 41
B1H6CCW | 40
B1H9CW | 6
C1H12CCW | 118
C1H3CW | 83
C1H3CCW | 81
C1H6CW | 43
C1H6CCW | 41
C1H9CW | 7
A1M3CW | 77
A1M3CCW | 77
A1M6CW | 39
A1M6CCW | 42
A1M9CW | 6
B1M12CCW | 112
B1M3CW | 73
B1M3CCW | 76
B1M6CW | 40
B1M6CCW | 40
B1M9CW | 7
C1M12CCW | 126
C1M3CW | 90
C1M3CCW | 85
C1M6CW | 45
C1M6CCW | 47
C1M9CW | 12
C2H12CCW | 119
C2H9CW | 12
A2M6CCW | 43
A2M9CW | 8
B2M12CCW | 116
B2M6CW | 37
B2M6CCW | 39
B2M9CW | 2
C2M12CCW | 128
C2M9CW | 15
A3H3CW | 88
A3H3CCW | 88
A3H6CW | 51
A3H6CCW | 50
A3H9CW | 18
B3H12CCW | 120
B3H3CW | 84
B3H3CCW | 83
B3H6CW | 45
B3H6CCW | 48
B3H9CW | 12
C3H12CCW | 120
C3H3CW | 79
C3H3CCW | 77
C3H6CW | 42
C3H6CCW | 42
C3H9CW | 11
A3M3CW | 80
A3M3CCW | 81
A3M6CW | 48
A3M6CCW | 47
A3M9CW | 15
B3M12CCW | 117
B3M3CW | 79
B3M3CCW | 79
B3M6CW | 45
B3M6CCW | 45
B3M9CW | 10
C3M12CCW | 122
C3M3CW | 80
C3M3CCW | 83
C3M6CW | 43
C3M6CCW | 40
C3M9CW | 10
A4H6CCW | 45
A4H9CW | 13
B4H12CCW | 123
B4H6CW | 51
B4H6CCW | 49
B4H9CW | 18
C4H12CCW | 125
C4H9CW | 16
A4M6CCW | 37
A4M9CW | 5
B4M12CCW | 118
B4M6CW | 50
B4M6CCW | 49
B4M9CW | 13
C4M12CCW | 120
C4M9CW | 14
A5H3CW | 83
A5H3CCW | 84
A5H6CW | 50
A5H6CCW | 46
A5H9CW | 13
B5H12CCW | 120
B5H3CW | 85
B5H3CCW | 83
B5H6CW | 48
B5H6CCW | 46
B5H9CW | 15
C5H12CCW | 125
C5H3CW | 88
C5H3CCW | 92
C5H6CW | 54
C5H6CCW | 55
C5H9CW | 24
A5M3CW | 85
A5M3CCW | 90
A5M6CW | 55
A5M6CCW | 54
A5M9CW | 18
B5M12CCW | 122
B5M3CW | 87
B5M3CCW | 87
B5M6CW | 52
B5M6CCW | 50
B5M9CW | 17
C5M12CCW | 122
C5M3CW | 84
C5M3CCW | 85
C5M6CW | 45
C5M6CCW | 48
A6H6CCW | 45
A6H9CW | 8
B6H12CCW | 123
B6H6CW | 50
B6H6CCW | 50
B6H9CW | 19
C6H12CCW | 125
C6H9CW | 27
A6M6CCW | 53
A6M9CW | 20
B6M12CCW | 118
B6M6CW | 45
B6M6CCW | 48
B6M9CW | 15
C6M12CCW | 123
C6M9CW | 25
A7H3CW | 78
A7H3CCW | 78
A7H6CW | 43
A7H6CCW | 43
A7H9CW | 12
B7H12CCW | 117
B7H3CW | 95
B7H3CCW | 83
B7H6CW | 55
B7H6CCW | 51
B7H9CW | 28
C7H12CCW | 118
C7H3CW | 85
C7H3CCW | 85
C7H6CW | 50
C7H6CCW | 50
C7H9CW | 17
A7M3CW | 86
A7M3CCW | 86
A7M6CW | 53
A7M6CCW | 51
A7M9CW | 23
B7M12CCW | 119
B7M3CW | 87
B7M3CCW | 87
B7M6CW | 53
B7M6CCW | 50
B7M9CW | 20
C7M12CCW | 120
C7M3CW | 90
C7M3CCW | 90
C7M6CW | 55
C7M6CCW | 55
C7M9CW | 22
A8H6CCW | 56
A8H9CW | 30
B8H12CCW | 123
B8H6CW | 53
B8H6CCW | 57
B8H9CW | 23
C8H12CCW | 118
C8H9CW | 21
A8M6CCW | 52
A8M9CW | 19
B8M12CCW | 122
B8M6CW | 54
B8M6CCW | 57
B8M9CW | 24
C8M12CCW | 119
C8M9CW | 23

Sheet: Angles for code
Angles for code
Servo Board and Pin Assignments |  |  | Angles for each for each position. These are pulled from the calibration table. No need to edit. |  |  |  |  |  |  |  |  |  |  |  |  |  |  |  | Combined servo names and positions for lookup table. Do not edit.
Change only if you use different pins |  |  | 1st digit |  |  |  | 2nd digit |  |  |  | 3rd digit |  |  |  | 4th digit |  |  |  | 1st digit |  | 2nd digit |  | 3rd digit |  | 4th digit
Servo | Board | Pin | Number | Servo | Position | Angle | Number | Servo | Position | Angle | Number | Servo | Position | Angle | Number | Servo | Position | Angle | Number | Servo & Pos | Number | Servo & Pos | Number | Servo & Pos | Number | Servo & Pos
A1H | 1 | 5 | 0 | A1M | 6CW | 39 | 0 | B3M | 6CW | 45 | 0 | B5M | 6CW | 52 | 0 | B7M | 6CW | 53 | 0 | A1M6CW | 0 | B3M6CW | 0 | B5M6CW | 0 | B7M6CW
A1M | 1 | 4 |  | B1H | 12CCW | 117 |  | C3H | 12CCW | 120 |  | C5H | 12CCW | 125 |  | C7H | 12CCW | 118 |  | B1H12CCW |  | C3H12CCW |  | C5H12CCW |  | C7H12CCW
A2H | 1 | 11 |  | B2M | 6CCW | 39 | 1 | A3H | 7CW | 35 |  | A6H | 6CCW | 45 | 1 | A7H | 7CW | 28 |  | B2M6CCW | 1 | A3H7CW |  | A6H6CCW | 1 | A7H7CW
A2M | 1 | 10 |  | C2H | 12CCW | 119 |  | A3M | 7CW | 32 |  | B6H | 12CCW | 123 |  | A7M | 7CW | 38 |  | C2H12CCW |  | A3M7CW |  | B6H12CCW |  | A7M7CW
A3H | 2 | 1 | 1 | A1H | 7CW | 19 |  | B3H | 7CW | 29 |  | B6M | 6CCW | 48 |  | B7H | 7CW | 42 | 1 | A1H7CW |  | B3H7CW |  | B6M6CCW |  | B7H7CW
A3M | 2 | 0 |  | A1M | 7CW | 23 |  | B3M | 7CW | 28 | 1 | A5H | 7CW | 32 |  | B7M | 7CW | 37 |  | A1M7CW |  | B3M7CW | 1 | A5H7CW |  | B7M7CW
A4H | 2 | 7 |  | B1H | 7CW | 24 |  | C3H | 7CW | 27 |  | A5M | 7CW | 37 |  | C7H | 7CW | 34 |  | B1H7CW |  | C3H7CW |  | A5M7CW |  | C7H7CW
A4M | 2 | 6 |  | B1M | 7CW | 24 |  | C3M | 7CW | 27 |  | B5H | 7CW | 32 |  | C7M | 7CW | 39 |  | B1M7CW |  | C3M7CW |  | B5H7CW |  | C7M7CW
A5H | 2 | 13 |  | C1H | 7CW | 25 |  | A4M | 6CCW | 37 |  | B5M | 7CW | 35 |  | A8M | 6CCW | 52 |  | C1H7CW |  | A4M6CCW |  | B5M7CW |  | A8M6CCW
A5M | 2 | 12 |  | C1M | 7CW | 29 |  | C4M | 12CCW | 120 |  | C5H | 7CW | 39 |  | C8M | 12CCW | 119 |  | C1M7CW |  | C4M12CCW |  | C5H7CW |  | C8M12CCW
A6H | 2 | 15 |  | A2M | 6CCW | 43 | 2 | A3H | 3CCW | 88 |  | C5M | 7CW | 30 | 2 | A7H | 3CCW | 78 |  | A2M6CCW | 2 | A3H3CCW |  | C5M7CW | 2 | A7H3CCW
A6M | 2 | 14 |  | C2M | 12CCW | 128 |  | A3M | 3CCW | 81 |  | A6M | 6CCW | 53 |  | A7M | 3CCW | 86 |  | C2M12CCW |  | A3M3CCW |  | A6M6CCW |  | A7M3CCW
A7H | 3 | 9 | 2 | A1H | 3CCW | 73 |  | B3H | 3CCW | 83 |  | C6M | 12CCW | 123 |  | B7H | 3CCW | 83 | 2 | A1H3CCW |  | B3H3CCW |  | C6M12CCW |  | B7H3CCW
A7M | 3 | 8 |  | A1M | 3CCW | 77 |  | B3M | 6CCW | 45 | 2 | A5H | 3CCW | 84 |  | B7M | 6CCW | 50 |  | A1M3CCW |  | B3M6CCW | 2 | A5H3CCW |  | B7M6CCW
A8H | 3 | 15 |  | B1H | 3CCW | 77 |  | C3H | 12CCW | 120 |  | A5M | 3CCW | 90 |  | C7H | 12CCW | 118 |  | B1H3CCW |  | C3H12CCW |  | A5M3CCW |  | C7H12CCW
A8M | 3 | 14 |  | B1M | 6CCW | 40 |  | C3M | 3CCW | 83 |  | B5H | 3CCW | 83 |  | C7M | 3CCW | 90 |  | B1M6CCW |  | C3M3CCW |  | B5H3CCW |  | C7M3CCW
B1H | 1 | 3 |  | C1H | 12CCW | 118 |  | A4M | 9CW | 5 |  | B5M | 6CCW | 50 |  | A8M | 9CW | 19 |  | C1H12CCW |  | A4M9CW |  | B5M6CCW |  | A8M9CW
B1M | 1 | 2 |  | C1M | 3CCW | 85 |  | B4M | 9CW | 13 |  | C5H | 12CCW | 125 |  | B8M | 9CW | 24 |  | C1M3CCW |  | B4M9CW |  | C5H12CCW |  | B8M9CW
B2H | 1 | 9 |  | A2M | 9CW | 8 |  | C4H | 9CW | 16 |  | C5M | 3CCW | 85 |  | C8H | 9CW | 21 |  | A2M9CW |  | C4H9CW |  | C5M3CCW |  | C8H9CW
B2M | 1 | 8 |  | B2M | 9CW | 2 |  | C4M | 9CW | 14 |  | A6M | 9CW | 20 |  | C8M | 9CW | 23 |  | B2M9CW |  | C4M9CW |  | A6M9CW |  | C8M9CW
B3H | 1 | 15 |  | C2H | 9CW | 12 | 3 | B3M | 3CCW | 79 |  | B6M | 9CW | 15 | 3 | B7M | 3CCW | 87 |  | C2H9CW | 3 | B3M3CCW |  | B6M9CW | 3 | B7M3CCW
B3M | 1 | 14 |  | C2M | 9CW | 15 |  | C3H | 3CW | 79 |  | C6H | 9CW | 27 |  | C7H | 3CW | 85 |  | C2M9CW |  | C3H3CW |  | C6H9CW |  | C7H3CW
B4H | 2 | 5 |  |  |  |  |  | C4H | 12CCW | 125 |  | C6M | 9CW | 25 |  | C8H | 12CCW | 118 |  |  |  | C4H12CCW |  | C6M9CW |  | C8H12CCW
B4M | 2 | 4 |  |  |  |  | 4 | A3H | 6CW | 51 | 3 | B5M | 3CCW | 87 | 4 | A7H | 6CW | 43 |  |  | 4 | A3H6CW | 3 | B5M3CCW | 4 | A7H6CW
B5H | 2 | 11 |  |  |  |  |  | A3M | 6CW | 48 |  | C5H | 3CW | 88 |  | A7M | 6CW | 53 |  |  |  | A3M6CW |  | C5H3CW |  | A7M6CW
B5M | 2 | 10 |  |  |  |  |  | B3H | 12CCW | 120 |  | C6H | 12CCW | 125 |  | B7H | 12CCW | 117 |  |  |  | B3H12CCW |  | C6H12CCW |  | B7H12CCW
B6H | 3 | 1 |  |  |  |  |  | C3H | 7CW | 27 | 4 | A5H | 6CW | 50 |  | C7H | 7CW | 34 |  |  |  | C3H7CW | 4 | A5H6CW |  | C7H7CW
B6M | 3 | 0 |  |  |  |  |  | C3M | 7CW | 27 |  | A5M | 6CW | 55 |  | C7M | 7CW | 39 |  |  |  | C3M7CW |  | A5M6CW |  | C7M7CW
B7H | 3 | 7 |  |  |  |  |  | A4M | 6CCW | 37 |  | B5H | 12CCW | 120 |  | A8M | 6CCW | 52 |  |  |  | A4M6CCW |  | B5H12CCW |  | A8M6CCW
B7M | 3 | 6 |  |  |  |  |  | B4M | 6CCW | 49 |  | C5H | 7CW | 39 |  | B8M | 6CCW | 57 |  |  |  | B4M6CCW |  | C5H7CW |  | B8M6CCW
B8H | 3 | 13 |  |  |  |  |  | C4M | 12CCW | 120 |  | C5M | 7CW | 30 |  | C8M | 12CCW | 119 |  |  |  | C4M12CCW |  | C5M7CW |  | C8M12CCW
B8M | 3 | 12 |  |  |  |  | 5 | A3H | 3CCW | 88 |  | A6M | 6CCW | 53 | 5 | A7H | 3CCW | 78 |  |  | 5 | A3H3CCW |  | A6M6CCW | 5 | A7H3CCW
C1H | 1 | 1 |  |  |  |  |  | C3H | 3CCW | 77 |  | B6M | 6CCW | 48 |  | C7H | 3CCW | 85 |  |  |  | C3H3CCW |  | B6M6CCW |  | C7H3CCW
C1M | 1 | 0 |  |  |  |  |  | C3M | 3CCW | 83 |  | C6M | 12CCW | 123 |  | C7M | 3CCW | 90 |  |  |  | C3M3CCW |  | C6M12CCW |  | C7M3CCW
C2H | 1 | 7 |  |  |  |  |  | A4H | 9CW | 13 | 5 | A5H | 3CCW | 84 |  | A8H | 9CW | 30 |  |  |  | A4H9CW | 5 | A5H3CCW |  | A8H9CW
C2M | 1 | 6 |  |  |  |  |  | A4M | 9CW | 5 |  | C5H | 3CCW | 92 |  | A8M | 9CW | 19 |  |  |  | A4M9CW |  | C5H3CCW |  | A8M9CW
C3H | 1 | 13 |  |  |  |  |  | B4H | 6CW | 51 |  | C5M | 3CCW | 85 |  | B8H | 6CW | 53 |  |  |  | B4H6CW |  | C5M3CCW |  | B8H6CW
C3M | 1 | 12 |  |  |  |  |  | B4M | 9CW | 13 |  | A6H | 9CW | 8 |  | B8M | 9CW | 24 |  |  |  | B4M9CW |  | A6H9CW |  | B8M9CW
C4H | 2 | 3 |  |  |  |  |  | C4M | 9CW | 14 |  | A6M | 9CW | 20 |  | C8M | 9CW | 23 |  |  |  | C4M9CW |  | A6M9CW |  | C8M9CW
C4M | 2 | 2 |  |  |  |  | 6 | B3M | 6CW | 45 |  | B6H | 6CW | 50 | 6 | B7M | 6CW | 53 |  |  | 6 | B3M6CW |  | B6H6CW | 6 | B7M6CW
C5H | 2 | 9 |  |  |  |  |  | C3H | 12CCW | 120 |  | B6M | 9CW | 15 |  | C7H | 12CCW | 118 |  |  |  | C3H12CCW |  | B6M9CW |  | C7H12CCW
C5M | 2 | 8 |  |  |  |  | 7 | A3M | 3CCW | 81 |  | C6M | 9CW | 25 | 7 | A7M | 3CCW | 86 |  |  | 7 | A3M3CCW |  | C6M9CW | 7 | A7M3CCW
C6H | 3 | 3 |  |  |  |  |  | B3H | 7CW | 29 |  |  |  |  |  | B7H | 7CW | 42 |  |  |  | B3H7CW |  |  |  | B7H7CW
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
